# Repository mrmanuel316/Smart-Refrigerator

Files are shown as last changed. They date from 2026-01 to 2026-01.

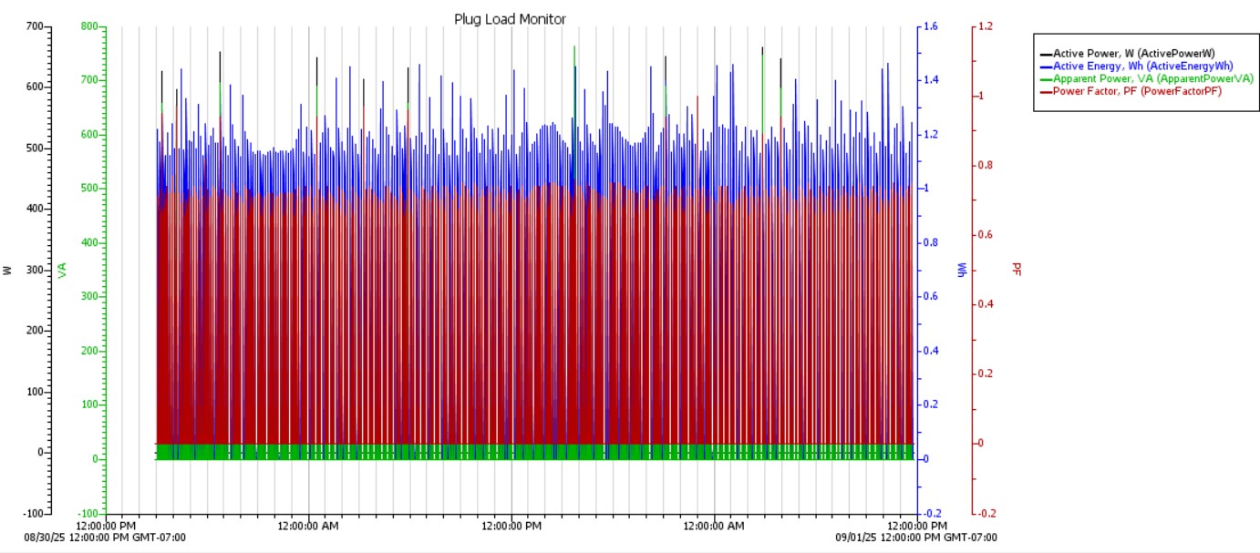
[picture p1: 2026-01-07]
Smart Refrigerator/Testing/Energy Performance/Only at Lvl 3 Power/First Test - No Bottle No Open/power graph.jpg

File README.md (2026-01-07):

# Smart Refrigerator – Passive Cooling Control System

## Demo Video
Watch the demo video on YouTube: [Smart Refrigerator Demo](https://youtu.be/O7e8nfwptJs)

## Overview
This project is an Arduino-based **Smart Refrigerator** system that automates cooling using fan-assisted heat dissipation and user-defined timing. It monitors temperature, controls fans, and provides real-time feedback through a digital display and buttons. The system is designed to improve energy efficiency during peak utility periods while maintaining safe internal temperatures.

## Project Objectives
- Automate cooling using fans and heatsinks  
- Monitor internal temperature in real time  
- Allow user input for time setting, manual override, and status control  
- Provide system feedback via digital display  
- Improve energy efficiency during peak usage periods  

## Hardware Components
- Arduino microcontroller  
- Temperature sensor (e.g., DS18B20)  
- Cooling fans and heatsinks  
- Digital display (7-segment or LCD)  
- Push buttons for time set, override, and control  
- Relays or transistor drivers  
- Power supply and wiring  

## Software and Tools
- Arduino IDE  
- C/C++ (Arduino)  
- Libraries for display and input handling  

## Data and Results
All experimental data, including temperature logs and performance results, are located in the `data/` folder (`Temperature_Data.xlsx`).

## Demonstration Videos
- Demo video stored locally: `media/Videos/Demo.mp4`  
- YouTube demo available at the top of this README.

## Project Images
Photos of the hardware setup, circuit, and final assembly are stored in `media/Images/`.

## Presentation Slides and Report
- Final technical report: `docs/Final_Report.pdf`  
- Presentation slides: `docs/Slides.pdf`  

## How It Works
1. Temperature sensor continuously monitors internal temperature  
2. Arduino reads the sensor data and compares it to predefined thresholds  
3. Fans activate automatically when cooling is required  
4. Users can manually set timing or override system using buttons  
5. System status and timing displayed in real time  
6. Safety logic prevents overheating or unsafe operation  

## Author
**Matthew Rabeje Manuel**  
Mechanical Engineering – San José State University  
Email: m.rmanuel003@gmail.com

## License
This project is for educational purposes. Free to use and modify with credit.

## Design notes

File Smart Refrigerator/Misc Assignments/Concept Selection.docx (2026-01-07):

Smart Refrigerator Concept Selection

Ideas considered for concept selection

Our group had a lot of ideas on how to execute building a mini fridge with a passive and active cycle. Some of the areas with the most variation were the fin and ice configuration, where in respect to the rest of the fridge would the fins, ice, and fans be located, as well as where to place our more complex control panel. During the concept creation phase, we had a lot of different ideas on how best to execute our envisioned project. However, there was a lot of overlap between designs, so it was quite easy to consolidate them to three or four well developed ideas. One way we consolidated or eliminated ideas was through evaluating the manufacturing cost. It was easy to get creative with different ice and fin designs, including circular tubes or curved banks of fins. However, once our group evaluated from a manufacturing perspective, some of our more abstract, yet efficient designs were eliminated.

After consolidating and eliminating ideas, we began to start discussing our options for the primary design decisions such as heat transfer shapes to contain our passive cooling ice block, control panel functions and placement, shelf designs, location and format of the control panel, and control panel location.

Control Panel Location

A control panel/apparatus is required for consumer use and monitoring. We plan to have a very simple setup where a user can see when their refrigerator is running an active/passive cycle, and we also plan to add a way for them to possibly override the passive cooling if desired. The control panel could be located on the front of the fridge, on the door of the fridge inside, or above the fridge door. Figure 1 shows three possible locations for our control panel.

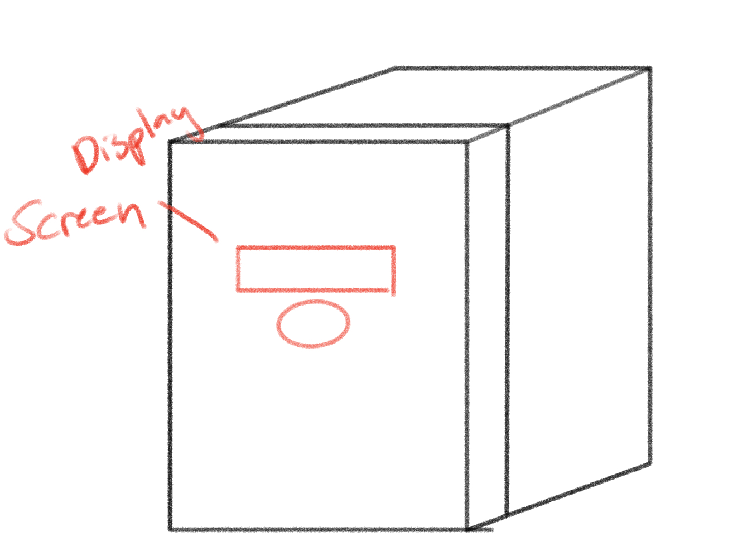
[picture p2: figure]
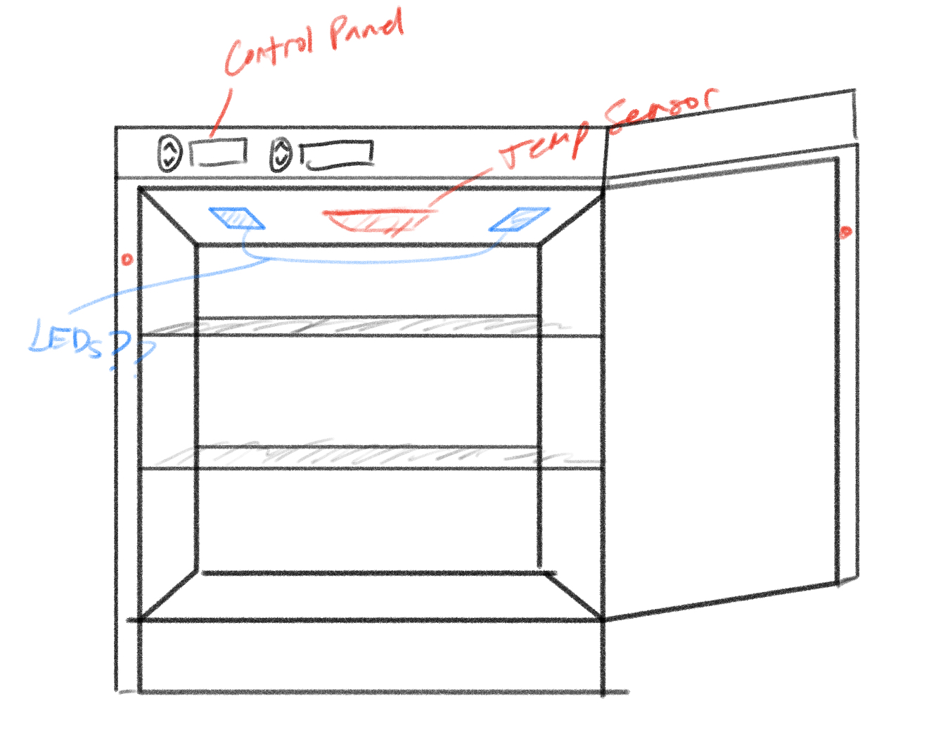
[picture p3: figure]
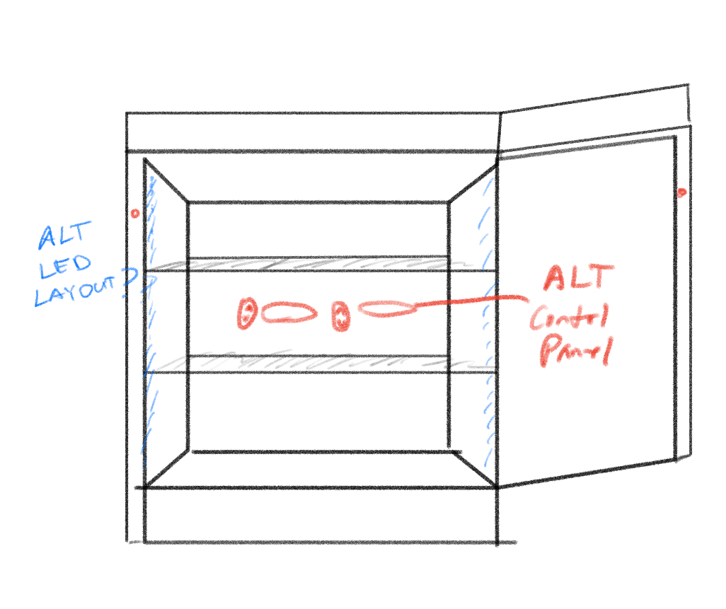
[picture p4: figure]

Figure 1. Alternative placement locations for refrigerators control panel

Control Display Layout

In our initial concept generation, we only had one concept generated for our potential control panel display layout as seen in Figure 2, so we just discussed how we would modify it to ensure we knew exactly what we wanted for our final design. To meet customer needs and make our fridge user friendly, a good control panel is needed, so we considered using lights, seven segments, or a LED screen.

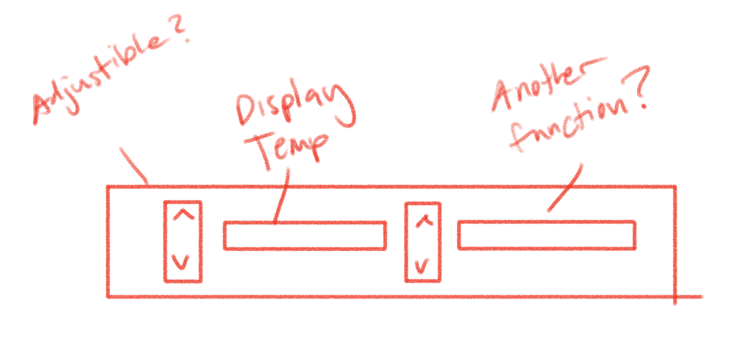
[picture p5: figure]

Figure 2 - Potential Display layout 1

Shelf Layout

During our customer needs survey, shelving and interior space was the most important metric for all respondents. Practically speaking, consumers want refrigerators to store food, so high-volume and convenient storage is important. With that said, the easiest way to optimize space for the consumer is to find an ideal shelving layout for our fridge. We introduced two options shown in figure three that have promise. Option one contains two bottom shelves, one large shelf, and one narrow shelf where option two contained two removable shelves, one drawer, a compartment for compressor/refrigerator components in the back, and rails for shelf adjustment.

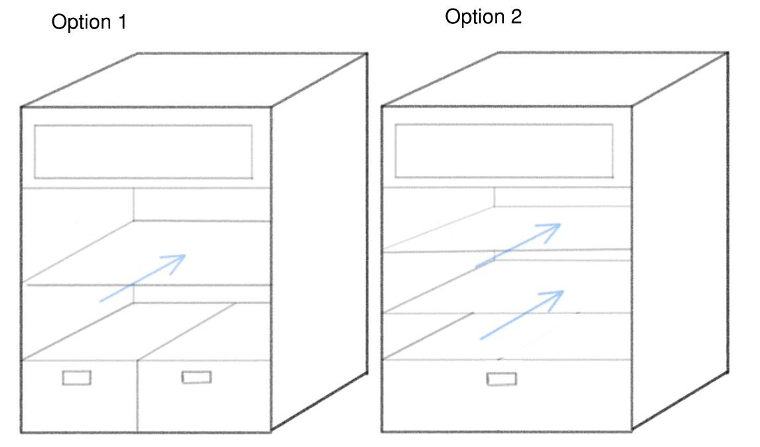
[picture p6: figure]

Figure 3 - Shelf Layout Options

Heat transfer Design

For the passive cooling cycle to provide effective cooling, air from the refrigerator must be cycled through a freezer compartment and cooled to below refrigeration temperature before it re-enters the refrigeration compartment. For cooling to occur, the air must interact with a medium that is at a lower temperature than the air itself such as ice. Only blowing air over ice would decrease the temperature of the air but is limited by the surface area. To increase the surface area and therefore improve the amount of heat transfer that occurs, fins made out of a highly conductive metal can be used. All blocks of ice will be similar to ice packs such that there will be water sealed inside a case with a gap of air so that the water can expand when it freezes and be contained when it melts.

We generated many different concepts for the form of the heat transfer component and created CAD models to better visualize and evaluate the designs. These concepts were constrained by whether the freezer compartment was located on top of the refrigeration compartment, increasing the refrigerator’s height or behind it, increasing the required floor space. Design 1 and Design 2 shown below in Figure 5 showcase the configuration where the freezer compartment is located on top of the refrigerator. Design 1 has one large slab of ice with a panel of fins located on the top and bottom. There would be a metal plate that constrains the air to flow either above or below the ice block through the fins. Design 2 is similar but instead uses several thin sheets of ice rather than one large block. This allows for more surface area to install fins and allow for air to flow through.

Design 3 through Design 5 showcase the configuration where the freezer compartment is located at the back of the refrigerator. Similar to Design 2, Design 3 includes several thinner sheets of ice with fins between. However, in Design 3 the sheets of ice are vertical. Though the vertical design allows for more surface area for heat transfer to occur, ice freezes much faster when it is placed in horizontal configurations. For this reason, Design 4 and 5 direct the airflow in a serpentine pattern such that the slabs of ice can be placed horizontally. Triangle wedges are used in the corners to decrease the backflow and pressure drop. Design 4 uses rectangular while Design 5 uses circular tubes.

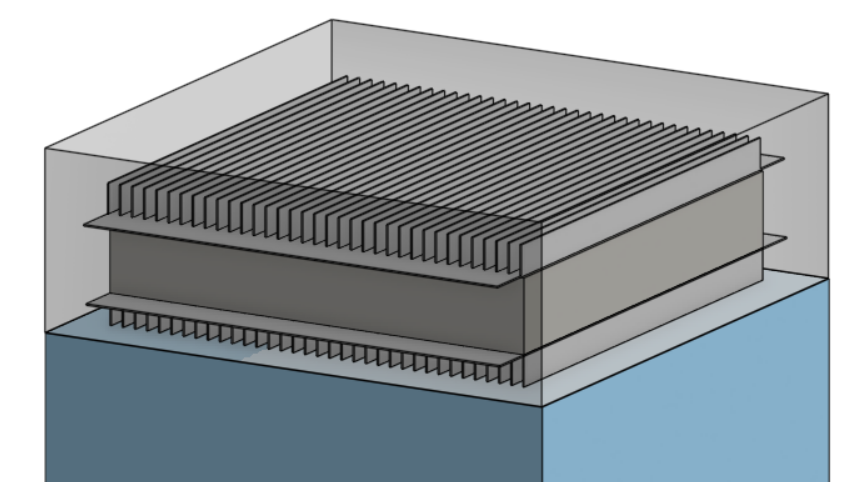
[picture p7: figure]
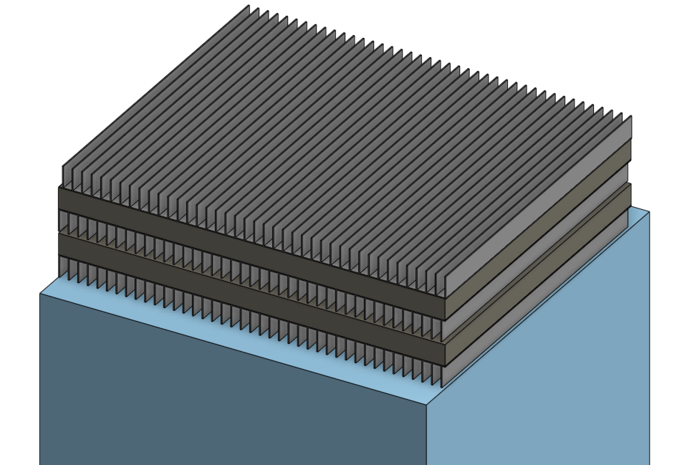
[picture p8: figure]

Design 1 | Design 2

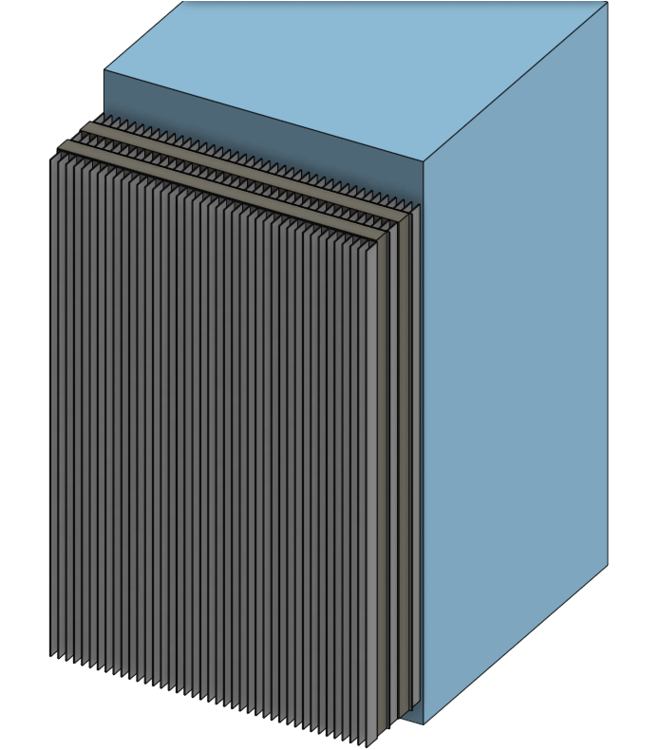
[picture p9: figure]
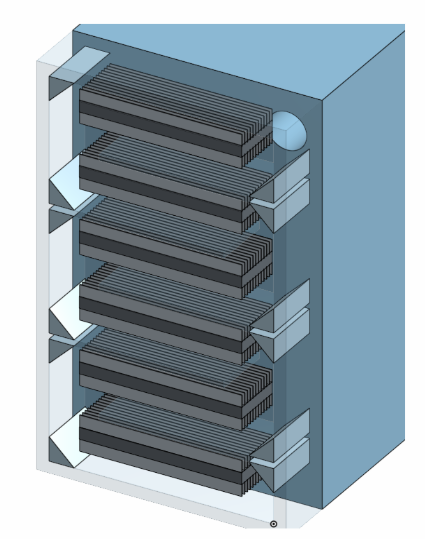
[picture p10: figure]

Design 3 | Design 4

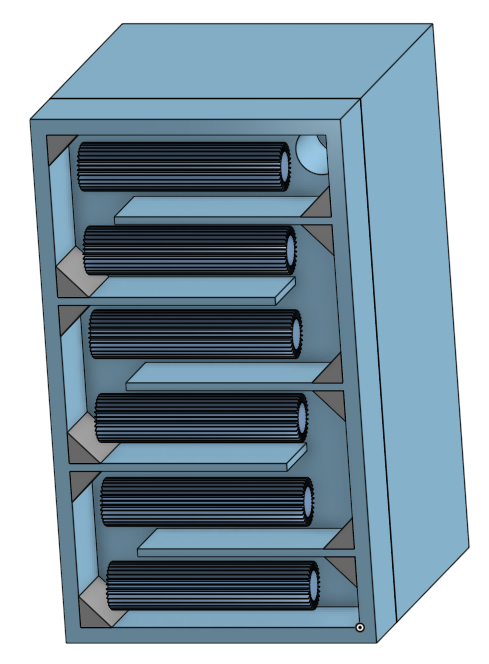
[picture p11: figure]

Design 5

Figure 4 - Heat transfer layout options

Decision Method used

Heat transfer

To choose which design was best for the heat transfer between ice and air, we used a Pugh matrix shown below in Table 1. We wanted to zero in on only the most relevant criteria that would affect feasibility of the project, such as manufacturability, efficient use of space, and heat transfer effectiveness. In terms of manufacturability, we found that most fins that can be purchased are meant to be installed on flat surfaces. This means that wrapping fins around a circular tube such as in Design 5 would be very difficult. Furthermore, we recognize that the serpentine pattern in Design 4 and 5 would be more challenging to construct compared to the simpler stack configuration in Design 1-3.

Since the passive cooling system relies on having a block of ice, the water must be frozen during the active cooling mode. To provide a net negative in energy consumption, the ice must be frozen and with as little energy as possible. For this reason, one of our criteria in the Pugh chart is how quickly the ice will freeze. This is dependent on the thickness of the block, the shape (rectangular vs circular) as well as the orientation of the block (horizontal vs vertical). Since Design 2 and Design 4 used thin, rectangular blocks that were horizontal, they had the best ice freezing rate and were awarded positive points accordingly. Though Design 1 is also rectangular and horizontal, freezing one large block rather than multiple thin layers will take longer.

Another aspect of the effectiveness of our refrigerator is how much electricity the system will consume during peak hours while the system is in passive cooling mode. During this mode, the only component that will be active is a fan that pushes air through the freezer compartment to decrease its temperature. The size of the fan will be dependent on the airflow pattern as well as how much surface area is available in the fins for heat transfer to occur. Design 1-3 all have simple airflow patterns which is ideal. The serpentine aspect of Design 4 and 5, however, is poor for airflow and would require a larger motor on the fan to overcome the loss in static pressure due to the turbulence in the turns. The size of the fan is also dependent on the fin surface area because increasing the surface area that is available for heat transfer to occur will cause the outlet temperature to be lower. The refrigerator will require less air circulation if it is supplied at a cooler temperature, allowing the fan to run at a lower speed and draw less electricity. For this reason, Design 2 - 4 which all had thin layers with lots of fin surface area are more desirable for our final design.

Finally, the amount of space that the freezer compartment requires is very important as it relates to the amount of usable interior storage space given a limited exterior size. From our evaluation of customer needs, it is clear that adequate interior space is very important for our customers. Since the ice blocks in Design 1-3 are pressed between fins with no wasted space or additional structure required, they make the most efficient use of space compared to Design 4-5. From the Pugh Chart, it is clear that the most ideal design is Design 2 with 5 points followed by Design 3 with 4 points. For this reason, we have chosen to move forward with Design 2.

Table 1: Pugh matrix for Heat Transfer Shapes

Criteria | Baseline/ Datum | Design 1 | Design 2 | Design 3 | Design 4 | Design 5
Ice freezing rate | 0 | 0 | +1 | -1 | +1 | -1
Fin Surface Area | 0 | -1 | +1 | +1 | +1 | 0
Manufacturability | 0 | +1 | +1 | +1 | 0 | -1
Efficient Use of Space | 0 | +1 | +1 | +1 | 0 | 0
Airflow Pattern/Static Pressure | 0 | +1 | +1 | +1 | -1 | -1
Total | | 2 | 5 | 4 | 1 | -3
Rank | | 3rd | 1st | 2nd | 4th | 5th

Control Panel

One of the main methods we used to determine the location of the control panel was to insert images from our concept generation into this document, organize them to better understand our options for each concept, and discuss what we think would work best for us in conjunction with our customer needs. Since we unanimously agreed that the best location for the control panel was located inside the refrigerator near the top of the refrigeration compartment, we didn’t need to use a decision making tool such as the Pugh Matrix.

To decide which indicators and controls should be included, we discussed the necessary interactions required between the microcontroller and the user. Since temperature control was not highly prioritized in our customer needs, we decided the control panel did not need up or down arrow buttons. The only inputs that are crucial for operation are that the user can tell the refrigerator when their utility rates and set the clock to accurately match the local time. The additional display features were then evaluated based on how crucial they were and what the user would like to know to troubleshoot any issues they encounter.

Shelf layout

To evaluate all of our shelf layout options, we placed the images side by side and discussed the pros and cons of each option. We once again referred to our customer needs and the importance of both the interior storage space and flexibility in shelving layout. When narrowing down our shelf design options, we also took into consideration the current shelf design of the broken mini fridge that we will be using as a starting point for our construction.

Final Concept

The final fin and ice configuration our group decided on was Design 2 for the freezer compartment. We chose this design using the Pugh chart as it had the highest score due to the high fin surface area, ideal freezing time, good airflow, efficient use of space and ease of constructability.

Figure 5 - Final design choice for fin and ice configuration

For the control panel configuration, we opted to not have user input for temperature. Because of the nature of our design, our refrigerator will not have a freezer, it will only keep things cold, so we felt user input was redundant to set temperature, our smart refrigerator will be programmed to maintain an internal temperature of 37 degrees fahrenheit. We did deem it important that our control panel will display the internal temperature. We also concluded it necessary for the control panel to indicate whether our project is on its active or passive cycle, which will be done with LED lights.

Lastly, for the user to configure when they want the passive cycle to run, we concluded on a design similar to conventional alarm clocks. We will have three time setting buttons, and two time adjustment buttons. The two time adjustment buttons are ‘hour’ and ‘minute’ and will be used to move the time around. The ‘clock set’ button will be used to set the primary clock time, this is the time that the passive cycle will start and end on. The user then will choose when they want the passive cycle to start and end. After discussing all the necessities for our control panel display, we came up with the display layout in figure 6.

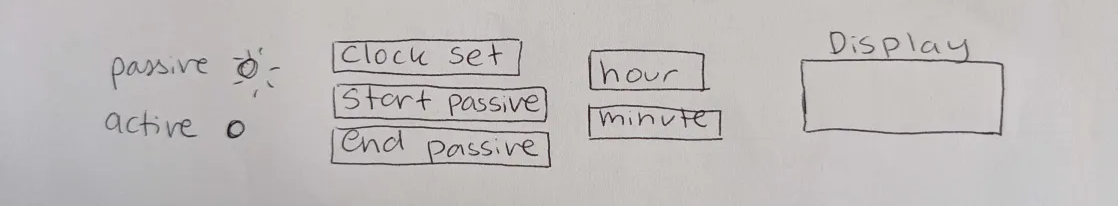
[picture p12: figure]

Figure 6 - Final control panel configuration

We also ultimately determined that the control panel should be placed on the top inside lip of the fridge as this is most custom and what most users are used to already as shown below in Figure 7.

Figure 7 - Final control panel location

For the shelving configuration, we decided to have two removable shelves and one single large drawer at the bottom shown below in Figure 8. This allows for the user to customize their refrigerator layout to best suit which items they regularly purchase and store. Furthermore, the single larger drawer rather than the two smaller drawers is better suited for our design because of the scale of the mini refrigerator we are working with.

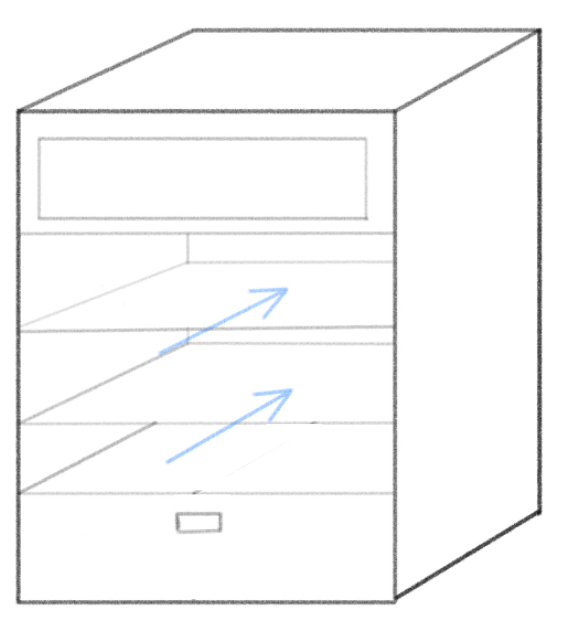
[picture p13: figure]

Figure 8 - Final shelf configuration

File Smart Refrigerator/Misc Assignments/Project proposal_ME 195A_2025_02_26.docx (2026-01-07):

Project Proposal

ME 195A, Spring 2025

Smart Refrigerator

Faculty Advisor: Dr. Keith Yi, keith.yi@sjsu.edu

Technical Advisor: Dr. Kabbani, hussameddine.kabbani@sjsu.edu

# Student Team Members (name, phone#, email)

1. | Isabel Price (team lead) | (669) 333-1464 | isabel.price@sjsu.edu
2. | Brent Marin | (650) 293-1821 | brent.marin@sjsu.edu
3. | Caleb Mok | (408)-309-3238 | caleb.mok@sjsu.edu
4. | Kalino Ruiz | (669) 333-1462 | kalino.ruiz@sjsu.edu
5. | Matthew Manuel | (408)-316-1427 | matthew.manuel@sjsu.edu

# Student Team:

1. Isabel Price | | | 3/18/2025
2. Brent Marin | | | 3/18/2025
3. Caleb Mok | | | 3/18/2025
4. Kalino Ruiz | | | 3/18/2025
5. Matthew Manuel | | | 3/18/2025

1. Introduction

With the knowledge we now have about various environmental problems centered around climate change, it is our duty to create a sustainable world and minimize our carbon footprint. One way we can do this is by reducing the average household energy expenses with the help of energy efficient appliances. By leveraging active and passive refrigerating techniques, we can incorporate a local ice storage system into a refrigerator that will generate ice during off peak hours which will maintain the internal temperature of the fridge during hours of peak electricity rates. Utility rates are how much we are charged for energy. When utility rates are higher during peak hours, we aim to use the passive cooling method to save the user money. The smart refrigerator intends to provide users with an eco-friendly and affordable option by decreasing utility rates and energy consumption.

2. Project Objectives

Our primary objectives include:

- Make an affordable, energy-efficient, and cost saving refrigerator
- The refrigerator must have easy to clean removable shelves
- A microcontroller will control the state of the refrigeration cycle

We want to build or repurpose a mini refrigerator that has an active and passive cooling cycle. The passive cycle relies on the principle of stored thermal mass to limit consuming energy during peak-load hours to save the consumer money. As a group we decided that our project will not be a success unless both active and passive cooling cycles work effectively. Lastly we want to retain as much of the original insulation in our mini refrigerator.

3. Customer Requirements

As a group we conducted a survey to get feedback on what people are looking for regarding refrigerators. We had 22 responses, with ages from 18 to 55+, about 54% of our responses were women and the rest were men. Once we received our input, as a team, each group member weighed each need on their own. The three highest customer needs for a refrigerator were: interior storage space, durability, and that it is easy to clean. Within our team, the three highest needs were interior storage space, the cost of the product, and the energy usage. The full customer needs results can be found below in Appendix B.

4. Background Research

Though there are not any currently commercially available refrigerators with integrated passive cooling methods, there have been studies conducted on refrigerator prototypes, refrigerated transport boxes, and air conditioning systems that use various methods of passive cooling. Garber-Slaght of the Cold Climate Housing Research Center conducted an experiment comparing regular refrigerators to a prototype unit with thermal fins located outside of the building, exposed to the winter conditions (2013). The results showed that the retrofit prototype unit used 6.3 kWh compared to 36.1 kWh for the regular units during the winter, though it underperformed during the summer due to the fins absorbing additional heat rather than cooling. This shows that passive refrigerator models can be effective in saving consumers money.

Other technologies and prototypes exist that use thermal mass as a means of either maintaining refrigerated temperatures for durations of time. Fauer and Cremaschi developed a transport box for blood bags that successfully maintained the temperature between 2 and 6 ℃ for an extended period of time using only phase change materials as a form of thermal mass (2024). Our Smart Refrigerator will be a combination of these technologies as it will integrate the thermal mass method of refrigeration boxes into the typical form of a refrigerator with a refrigerant loop and compressor.

5. Design Constraints

There are four main constraints regarding our project. They are: budget limitations, material availability, safe operation, and sound levels produced. Funding is limited from our sponsors and the members of this group have a limit they are willing to spend individually. Regarding the construction of the insulation of our project, some materials are far better at insulating heat than others, but are not always readily available for sale to the public nor cheap. When it comes to prototyping our project, consumer safety is our number one priority so we will be avoiding flammable refrigerants.Our last constraint is sound level, this mainly pertains to the compressor. While it may be more cost and power efficient to go with a cheap, large, or low quality compressor, we want to design a product that consumers will use and not notice.

6. Project Plan & Gantt Chart

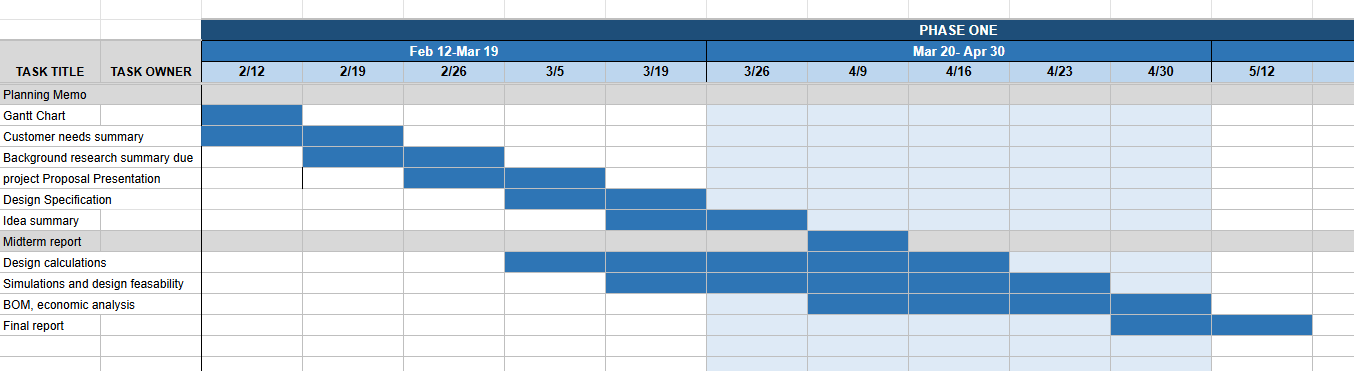
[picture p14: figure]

We aim to work as a team toward the final report for the semester. Our work is currently split between technical leads who will be in charge of CAD, heat transfer calculations, fabrication, code, the refrigeration cycle, and mechatronics/sensing. We still plan to have all team members help each other on their lead assignments. Strong communication is a cornerstone of all work to be done. Our general strategy is to work ahead of time on as many assignments as is reasonably possible, which is why we have already started rough design calculations and economic analysis, as both go hand-in-hand with testing the viability of our project.

References

Fauer, C., & Cremaschi, L. (2024). Passive cooling of two phase change materials installed in series. International Journal of Refrigeration, 159, 124–133. https://doi.org/10.1016/j.ijrefrig.2023.12.024

Garber-Slaght, R. (2013, March). Passive Refrigeration. Cold Climate Housing Research Center; CCHRC. https://cchrc.org/wp-content/uploads/media/passiverefrigeration.pdf

Appendices

A. Mission Statement
B. Customer Needs Summary
C. Teamwork Plan

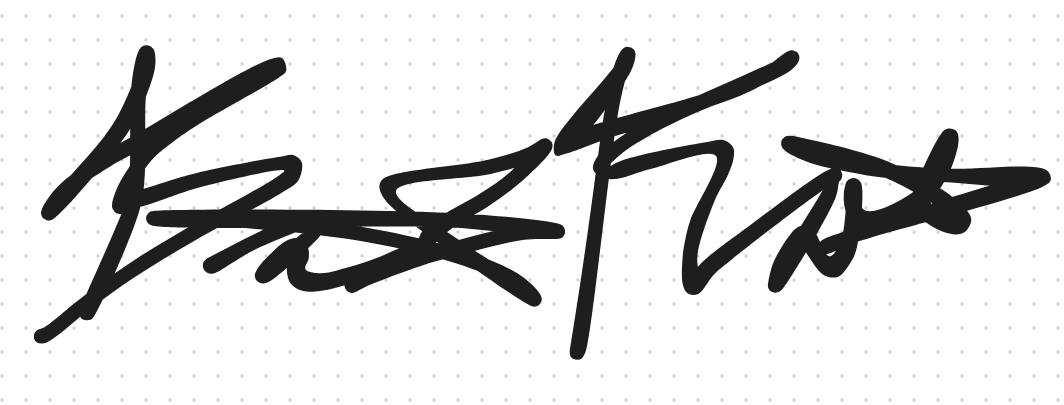
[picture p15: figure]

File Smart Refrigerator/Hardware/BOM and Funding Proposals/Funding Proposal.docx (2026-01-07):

Smart Refrigerator

Isabel Price, Kalino Ruiz, Matthew Manuel, Brent Marin, Caleb Mok

ME 195A Section 02

Instructor: Dr. Keith Yi

Technical Advisor: N/A

5/9/2025

Executive Summary

In California, the cost of electricity is continuously rising, leading to more households and individuals being unable to afford their electricity bills. Typical rate schedules for electricity costs have a peak period in which the price of electricity is increased due to the high demand during that time of the day. One method of reducing electricity cost in cooling systems is to shift the consumption of electricity from the peak time to off-peak through thermal mass.

Our product, the Smart Refrigerator, is a mini refrigerator that utilizes thermal mass in the freezer chamber with the purpose of shifting electricity consumption from peak to off-peak periods to save the user money. This prototype will involve the retrofitting of an existing mini refrigerator. Our goal is to successfully integrate the passive cooling system involving the thermal mass, heat sinks, and fans, with the existing active refrigeration system such that the refrigerator can still operate regularly during off-peak hours.

The mini refrigerator will be controlled with a microcontroller that will monitor temperatures throughout the chamber and control the switch between the active and passive cooling modes based on the user's rate schedule. Our expected outcome is a fully operational mini refrigerator that responds to user inputs for their personal rate schedule. The project will be successful if both the unmodified active refrigeration system and the added passive refrigeration system maintain a refrigeration temperature of 37 degrees and provide cost savings for the user.

Anticipated Deliverables

Our final anticipated deliverable is the physical prototype of the retrofitted mini refrigerator that is capable of using passive cooling for several hours a day and maintains the storage chamber at a safe refrigeration temperature. This fabrication process can be broken down into smaller deliverables including the repair of the existing broken mini refrigerator we are retrofitting, the lowering of the freezer compartment, construction of the heat sink and ice block assembly, and the installation of the various aluminum plates to direct air flow. Furthermore, the implementation of the microcontroller and sensors to effectively monitor the temperatures and control the refrigerator is an important step in the process. Along with the prototype, we will also provide data on the performance and energy cost savings to evaluate the success of the project.

This product will be beneficial for those who are interested in saving money on electricity throughout the year. It will be most cost-effective in states where electricity is expensive, such as in Hawaii or California. Furthermore, the Smart Refrigerator offers a cost-saving solution for college students and other young renters who are more likely to use a mini refrigerator and are particularly vulnerable to high electricity bills due to lower or inconsistent income.

Brief description and the most recent illustration of your latest design

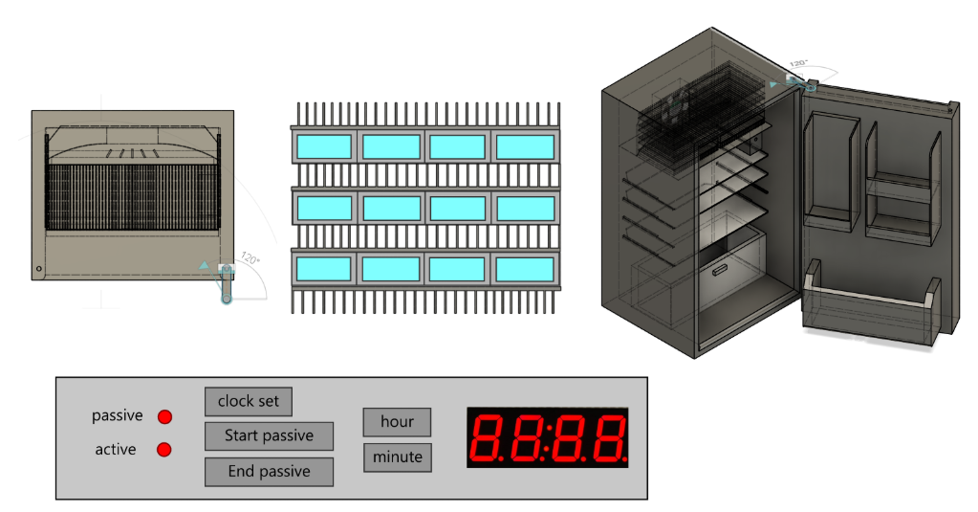
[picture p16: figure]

Figure 1 - Smart Refrigerator final design including freezer compartment layout, fin and ice block assembly, retrofitted mini refrigerator, and control panel layout

Our smart refrigerator will be programmed to maintain an internal temperature of 37 degrees Fahrenheit. We determined that the control panel should be placed on the top inside lip of the fridge, as this is what is most common. We will also be using LED lights for the control panel to indicate whether our project is on its active or passive cycle. The user will also be able to configure when they want the passive cycle to start and end with time setting adjustment buttons which work similarly to an alarm clock. There will also be LED lights that indicate whether it is on its active or passive cycle. Our control panel design layout is shown in the bottom image of Figure 1.

For the fin and ice configuration, our group decided on the design in the image in the middle. There will be four layers of fins to enhance heat transfer, along with three layers of ice to maintain the surface temperature at 0 degrees Celsius. For the ice containers, we will be using aluminum rectangular tubing with four individual tubes for each of the three thermal mass layers.

Since we will be using the freezer section for our thermal mass and passive cycle, we decided to direct airflow with a fan through the middle of the top back panel of the freezer to maximize convection. To further direct and smooth the air flow, we will also be using five vanes and curved sheet metal at the fan opening. This layout is shown in the top left corner of Figure 1.

Project Budget and complete rationale

Table 1 - Bill of Materials

Component Name | MFG# | Description/ Purpose | Quantity | Cost/ Unit | Shipping | Total | Notes | Link
Fan | SP100A | 4.68 Inch AC Tube Axial | 1 | 13.95 | $ 9.18 | $ 23.13 | Meets CFM requirement | Link (https://www.jameco.com/z/SP100A-1123XBT-GN-Sunon-120mm-115-VAC-60Hz-Ball-Bearing-Fan-240mA-20W-117-CFM_102884.html)
R134a Recharge kit | B09S69H5DP | To pressurize and add pipe length | 1 | 20.99 | $ - | $ 20.99 | Will need can of R-134a | Link (https://www.amazon.com/FANOVO-Refrigerator-Recharge-Refrigerant-Self-Sealing/dp/B09S69H5DP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)
R-134A | SER134A | Pure R-134A | 1 | 14.00 | $ 11.32 | $ 25.32 | | Link (https://coldhose.com/products/r134a-refrigerant-12oz-can?variant=35532320014496)
Copper Pipe | 630456606893 | Refrigerant Piping 3/8" OD | 1 | 16.99 | $ - | $ 16.99 | 5 Feet of tubing | Link (https://www.amazon.com/GOORY-Copper-Tubing-0-328-Refrigeration/dp/B0DKT3JDPT)
Heatsink | 64AS | 7.874'' (200mm) Wide Heatsink (64AS) | 8 | 9.90 | $ 12.36 | $ 91.56 | 7.9" x 6" | Link (https://heatsinkonline.com/products/7874-wide-heatsink-64as?variant=42105916653730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)
Temperature Sensor | ERP 2188820 | Refrigerator Thermistor | 2 | 11.00 | $ - | $ 22.00 | | Link (https://www.amazon.com/ER2188820-ERP-Thermistor-Replaces-2188820/dp/B01M8OFHHX)
Display | TM1637 | 4 Digit 7 Segment Display | 1 | 3.95 | $ 4.09 | $ 8.04 | | Link (https://www.jameco.com/z/TM1637-JVP-Jameco-ValuePro-TM1637-4-Bits-Digital-Red-LED-Display-Module-for-Arduino-7-Segment-0-36-4-Digit-Clock-Anode-Serial-Driver-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)
Buttons | EK1019 | 6x6x4.3mm TACT Switch Push Button | 1 | 6.98 | $ - | $ 6.98 | (pack of 50) Purchasing separately | link (https://www.amazon.com/Gikfun-6x6x5mm-Switch-Button-Arduino/dp/B00R17XUFC?gQT=2)
Aluminum Tube | T34118 | Ice casings | 12 | 9.30 | $ 41.00 | $ 152.60 | 4x1x1/8"x6 Note this shipping rate covers both the tube and sheets | Link (https://www.metalsdepot.com/aluminum-products/aluminum-rectangle-tube?product=290)
Sheet Aluminum | S3063 | Ice Casings/ controlling airflow | 2 | 42.72 | | $ 85.44 | 24"x24"x1/16" | link (https://www.metalsdepot.com/aluminum-products/aluminum-sheet?product=381)
Microcontroller | ESP32 | Control the Fridge | 1 | 8.00 | $ - | $ 8.00 | Already owned | link (https://www.espressif.com/en/products/socs/esp32)

Total including already purchased buttons and microcontroller: $461.05

Total funding requested from the department: $446.07

Part justifications

Heat sink selection

After comparing calculations with and without a heat sink, we determined that a heat sink is required to provide adequate heat transfer between the ice block and the air passing through the freezer compartment. There were many factors involved in choosing the optimal heat sink, including the size restrictions of the small freezer compartment we were working with, the length vs width orientation of the heat sink, as well as the minimum airflow to achieve the desired heat transfer. To determine the required heat transfer to maintain refrigeration temperature, we calculated the heat transfer through the walls of the refrigerator in addition to the added groceries that were stimulated by the energy required to take cans of water from room temperature to refrigeration temperature. The load profile can be found below in Figure 2.

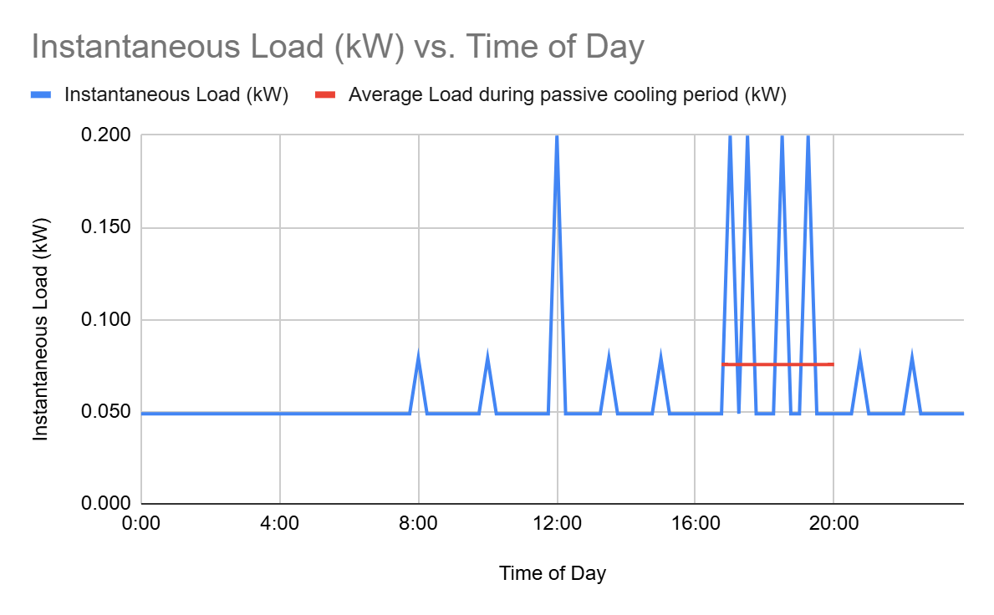
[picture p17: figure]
Chart

Figure 2 - Simulated instantaneous load on refrigerator cooling system

To choose the heat sink, we first created a tool in Google Sheets that used input dimensions of the heat sink and ice block, then calculated the resulting heat transfer given an input air flow rate. An example of the output calculations is shown below in Table 2. If the provided heat transfer rate was greater than the required heat transfer rate to maintain refrigeration temperature, the airflow was considered acceptable, as demonstrated by the green-filled cells in Table 2.

Table 2- Heat transfer calculations for heat sink

volumetric flow (CFM) | 20 | 30 | 50 | 55 | 60 | 70
V_dotTotal (m^3/s) | 0.00944 | 0.01416 | 0.02360 | 0.02596 | 0.02832 | 0.03304
Mdot Total (kg/s) | 0.01215 | 0.01822 | 0.03037 | 0.03340 | 0.03644 | 0.04251
V_dotPer fin (m^3/s) | 0.0000433 | 0.0000650 | 0.0001083 | 0.0001191 | 0.0001299 | 0.0001516
MdotPer fin (kg/s) | 0.000056 | 0.000084 | 0.000139 | 0.000153 | 0.000167 | 0.000195
Vair (m/s) | 0.408 | 0.612 | 1.020 | 1.122 | 1.224 | 1.427
Re | 295 | 442 | 737 | 811 | 885 | 1032
Flow | L | L | L | L | L | L
Entry Length | 0.156 | 0.233 | 0.389 | 0.428 | 0.467 | 0.545
Developed? | N | N | N | N | N | N
Nu | 4.42 | 4.74 | 5.30 | 5.43 | 5.55 | 5.79
h (W/m^2C) | 10.30 | 11.04 | 12.34 | 12.64 | 12.93 | 13.49
m | 4.06 | 4.20 | 4.44 | 4.50 | 4.55 | 4.64
fin efficiency | 88.94% | 88.26% | 87.08% | 86.82% | 86.57% | 86.08%
Toutlet (C) | 1.2 | 1.6 | 2.1 | 2.1 | 2.2 | 2.3
(Tbase-Tin) | 5.04 | 5.04 | 5.04 | 5.04 | 5.04 | 5.04
(Tout - Tsurf) | 1.1 | 1.5 | 2.0 | 2.1 | 2.2 | 2.3
Delta T LMTD | 2.6 | 3.0 | 3.3 | 3.4 | 3.4 | 3.5
Qfin, actual (W) | 31.9 | 38.5 | 47.4 | 49.2 | 50.8 | 53.9
Qdot diff | -18.60 | -12.02 | -3.11 | -1.33 | 0.33 | 3.38

The ultimate goal of this optimization process was to determine which heat sink had the best fin height, thickness, and spacing and how many layers of ice and fins were necessary to achieve a reasonable airflow rate. We chose the heat sink that had the optimal heat transfer when compared to six different heat sinks that varied in fin spacing and height. Next, we determined that three layers of ice were required with the chosen heat sink to obtain a reasonable average airflow rate of approximately 60 CFM.

Fan Selection

Before selecting our fan, we calculated the pressure drop at various air flow rates to create a system curve shown below in Figure 3. Then, we researched fans that had a maximum airflow rate that was about twice as large as our calculated average airflow. This would allow the passive system to respond to larger instantaneous loads and prevent the refrigerated space from exceeding the acceptable temperature range. We considered the fans' power consumption and size as these were the most important considerations. After choosing the fan that best met these criteria, we plotted the provided fan curve against our system curve to ensure that the fan was able to overcome the pressure drop it would encounter. Since the fan curve intersects the fan curve at a greater airflow than the minimum average airflow we calculated previously, we know that the fan will be adequate. We will modulate the fan to lower or higher speeds to meet the instantaneous airflow requirements.

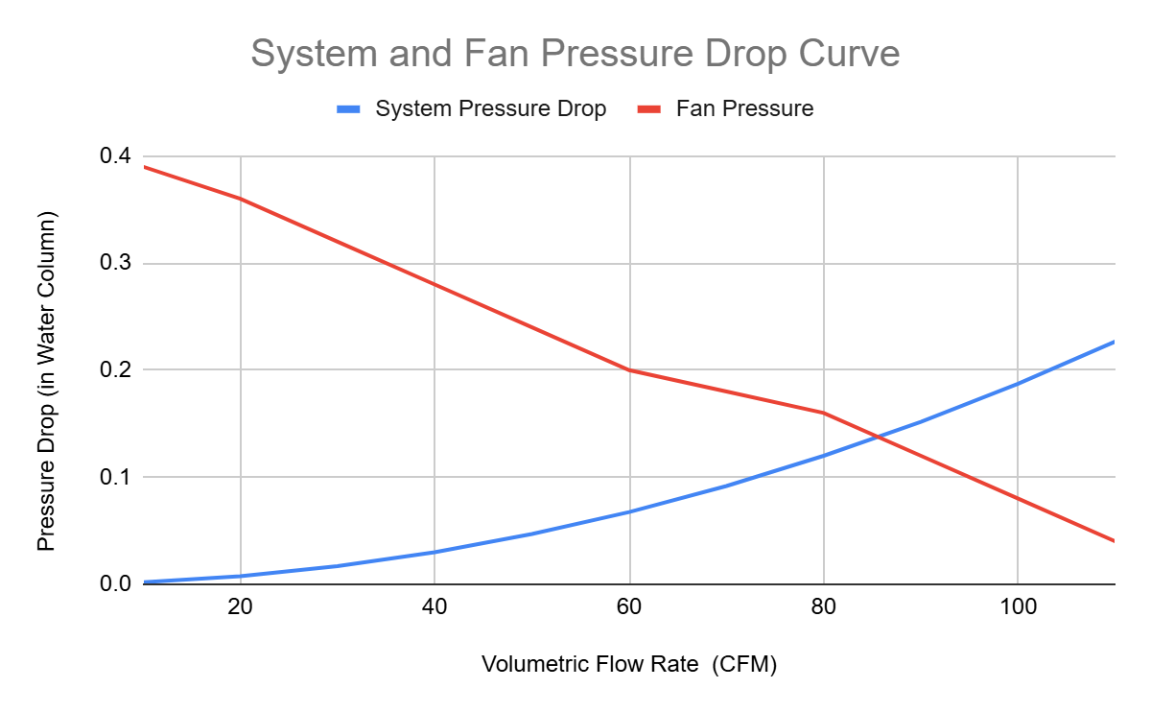
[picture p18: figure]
Chart

Figure 3 - System and Fan Pressure Curve

Ice Block Containers

We chose hollow aluminum tubes for our ice block containers instead of bending aluminum sheet metal for ease of fabrication and less potential for water leakage. By using tubing, we can create module ice cases by cutting the tube to the desired length, filling it with water, then welding an aluminum plate end cap on each end. We will utilize the aluminum plate for the end caps, as well as fashioning brackets to connect the fin/casing housings together in the freezer portion of our fridge. The last usages of our aluminum plate will be to create a return duct on the back wall of the inside of our mini refrigerator to return air to the fan to be cooled off during the passive cycle, as well as vanes and a wall to along the backside of the evaporator coils to direct airflow over the ice block casing assembly.

Electronic components

We decided to use the ESP32 microcontroller because of its vast capabilities and versatility. This microcontroller can be used as an efficient central processing unit capable of managing system inputs and outputs, sensors, and wireless communication. It is also a relatively fast processor with a speed of 240 MHz, which is more than sufficient for the system we’re planning to run. Additionally, it’s compatible with Arduino and MicroPython, the software that we’ve familiarized ourselves with in previous courses.

We chose the temperature sensors to be thermistors because of their high sensitivity to changes in temperature and their lower costs than alternative devices like thermocouples. Then we need a 7-segment display for our control panel that will display the time that the user selects for the start and stop of the passive cycle.

Return air ducting, fan ducting

To ensure that the air travels through all of the shelves rather than immediately re-entering the freezer compartment, we are installing a thin aluminum sheet to act as a return duct with a gap at the bottom of the refrigeration compartment. This requires a sheet of aluminum that will act as the return duct.

Within the freezer compartment itself, the air flow from the fan must be contained such that it flows through the fin + ice block assembly. To do this, we will be using aluminum sheets that are bent to fit into the corners of the freezer compartment. Furthermore, vanes will be used to disperse the fan flow to more equally distribute the flow through the individual fins. These vanes can be cut from the thin aluminum sheet as well.

Refrigerant piping

The freezer space in the mini refrigerator we are retrofitting only has a height of about 5 inches. However, the fin and ice block assembly has a height of 6.15 inches. In order for the fin and ice block assembly to fit, we must detach the evaporator coil and move it about 1.4 inches lower. We need a few inches of piping to account for this vertical translation. We chose the shortest amount of piping possible to save money; alas, the shortest length available was a 5-foot coil. In addition to this, because we are cutting the preexisting refrigerant piping, we need a way to pressurize and add more refrigerant after we drain it. We will be purchasing a kit that adds valves to hook up to a hose so that we can add refrigerant. This kit also comes with a pressure gauge, which will be very helpful so that we can ensure the compressor is operating smoothly. Lastly, we will be purchasing refrigerant to recharge the refrigerant line. Our mini-fridge requires 2.3 oz of R-134A, so we budgeted for a 12-oz. can.

Detailed Part List

The following is a list of the remaining parts that must be purchased for our project. Note that the microcontroller and buttons have already been purchased/owned by team members and do not need to be purchased by the department.

1. Aluminum Rectangle Tube
  a. Link (https://www.metalsdepot.com/aluminum-products/aluminum-rectangle-tube?product=290)
  b. Model: 4”x1”x1/8”
  c. Stock Number: T34118
  d. Dimensions: 4”x1” (1/ 8” thick) Choose cut to size, enter 6” Lengths
  e. Quantity: 12 Pieces
2. Aluminum Sheet
  a. Link (https://www.metalsdepot.com/aluminum-products/aluminum-sheet?product=381)
  b. Stock Number: S3063
  c. Dimensions: 2x2 Feet (1/16” thick)
  d. Quantity: 2
3. Aluminum heatsink
  a. Link (https://heatsinkonline.com/products/7874-wide-heatsink-64as?variant=42105916653730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)
  b. Model: 7.874'' (200mm) Wide Heatsink (64AS)
  c. Dimensions: Choose 6” length
  d. Quantity: 8
4. Refrigeration Piping Kit
  a. Link (https://www.amazon.com/FANOVO-Refrigerator-Recharge-Refrigerant-Self-Sealing/dp/B09S69H5DP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)
  b. Model: B09S69H5DP
  c. Dimensions: n/a
  d. Quantity: 1
5. Can of R-134A
  a. Link (https://coldhose.com/products/r134a-refrigerant-12oz-can?variant=35532320014496)
  b. Model: SER134A
  c. Dimensions: n/a
  d. Quantity: 1
6. Temperature Sensor
  a. Link (https://www.amazon.com/ER2188820-ERP-Thermistor-Replaces-2188820/dp/B01M8OFHHX)
  b. Model: ERP 2188820
  c. Dimensions: n/a
  d. Quantity: 2
7. Seven Segment Display
  a. Link (https://www.jameco.com/z/TM1637-JVP-Jameco-ValuePro-TM1637-4-Bits-Digital-Red-LED-Display-Module-for-Arduino-7-Segment-0-36-4-Digit-Clock-Anode-Serial-Driver-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)
  b. Model: TM1637
  c. Dimensions: n/a
  d. Quantity: 1
8. Fan
  a. Link (https://www.jameco.com/z/SP100A-1123XBT-GN-Sunon-120mm-115-VAC-60Hz-Ball-Bearing-Fan-240mA-20W-117-CFM_102884.html)
  b. Model: Sunon SP100A-1123XBT.GN
  c. Dimensions: 4.68 x 4.68 in
  d. Quantity: 1

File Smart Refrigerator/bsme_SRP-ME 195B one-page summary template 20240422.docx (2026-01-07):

Reducing Energy Costs Using Thermal Mass in Refrigerator

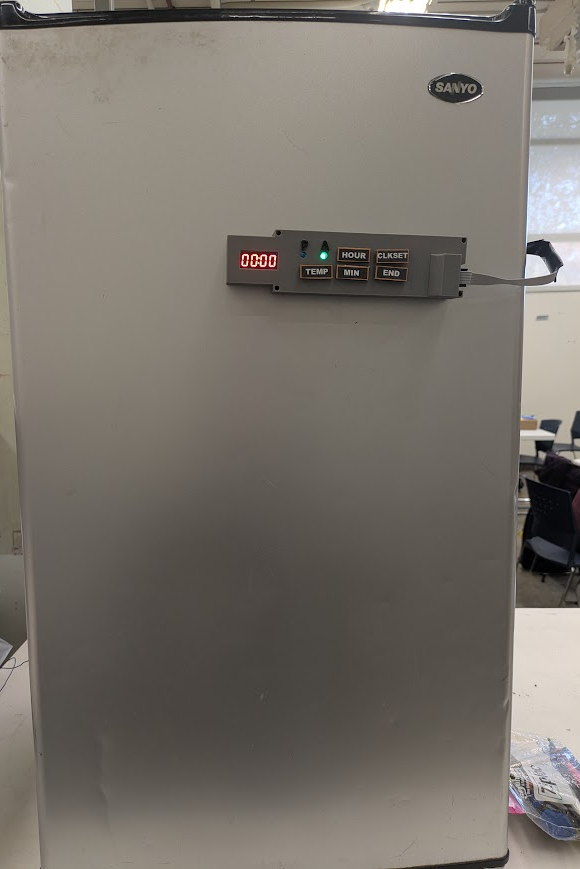
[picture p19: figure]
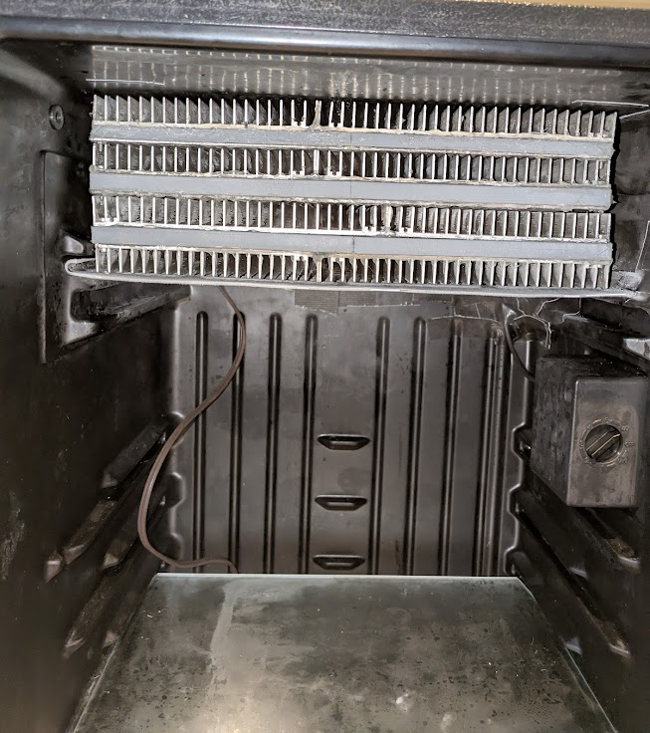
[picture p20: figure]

Student Team Members: Isabel Price (Lead) Matthew Manuel Brent Marin Caleb Mok Kalino Ruiz Faculty Advisors: Dr. Keith Yi Sargon Ishaya

Project Objectives:

We implemented a passive cycle assembly to a refrigerator that blows air over a thermal mass to maintain a safe internal temperature during the peak utility rates, reducing electricity cost, and a microcontroller to control the active and passive modes.

1. Utilize thermal storage to shift load away from peak time of use duration while maintaining safe refrigeration temperatures
2. Evaluate performance through energy consumption of both active and passive cooling cycles
3. Calculate money saved through minimizing energy usage during peak hours
4. Evaluate the air velocity profile of the passive cooling cycle

Significance:

This smart refrigerator improves environmental sustainability through reducing electricity load and carbon emissions during peak utility rate periods.

Project Results:

1. The fan successfully cycles on when the temperature is below 40°F until the chamber temperature lowers to 37°F.
2. The expected energy savings are 24.0 kWh/year based on initial tests.
3. The resulting cost savings are $12.60 per year.
4. The velocity profile was determined using an anemometer with an average velocity of 1.14 m/s.

Sponsors:

Thank you to Dr. Keith Yi, Sargon Ishaya, Desmond Cheung, Christopher Price, and Dr. Hussameddine Kabbani for their support throughout the design and fabrication of our senior design project.

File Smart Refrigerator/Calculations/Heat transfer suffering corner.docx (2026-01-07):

First step:

Estimate how volume of ice is required based on several different refrigeration load schedules

Step 2:

Create various different versions of the ice/fin model

Step 3:

For each version, determine fin surface area

https://www.mdpi.com/2079-6412/13/1/12

Step 4:

Determine if the fins can be considered constant temperature (find the temperature profile for fins of various lengths)

https://hedhme.com/content_map/?link_id=642&article_id=546

Although typical fin pitches are five to eight fins per centimeter, applications may exist for as many as 1,200 fins per meter in automotive applications. Fin thicknesses of 0.1–0.25 mm are common. Fin heights may range from 0.25 to 2 cm. A plate-fin exchanger with 600 fins per meter provides about 1,300 m²/m³ of heat transfer surface per cubic meter of volume. Such a heat exchanger would contain 10 times as much heat transfer surface per unit volume as in a typical shell-and-tube heat exchanger having 19 mm diameter tubes. Operated at a frontal velocity of 3 m/s, the heat transfer coefficient based on prime surface area would be on the order of 1,800 W/m² K.

Step 4:

Determine the heat transfer for given mass flow rate/outlet temperatures

Other things we need to figure out:

How are we going to tell the compressor when to turn on/off?

How are we going to control the power level of the compressor? (Duty Cycle - programming)

How are we going to control the power level of the fan? (Speed controller programming)

How will the air flow through the refrigerator

Where should the supply vent be located

How many vents should we use

Where should the return vent be located

What are we doing with the door of the refrigerator (shelves)

Are we going to put the heat exchanger in a new compartment on top of the refrigerator i inside the refrigerator (Kalino-y stuff)

Brent

- How do we freeze the ice

Matthew

- We need to make a circuit diagram that includes the fans, compressor, microcontroller, and sensors
- What microcontroller are we going to use?
- How is the microcontroller going to be powered
- We need to step down the voltage from the wall power supply
- We need a transformer?

Matthew

- Where should the temperature sensors be located?
- What type of temperature sensor should we use?
- How will the temperature sensor be installed?

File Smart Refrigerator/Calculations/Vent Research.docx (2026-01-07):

https://theappliancepros.ca/blog/refrigerator-return-air-vent/

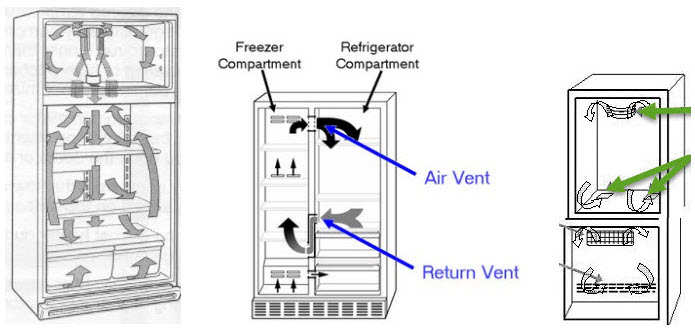
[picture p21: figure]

- PREDICTING AIRFLOW AND TEMPERATURE PATTERN INSIDE A REFRIGERATOR THROUGH CFD https://www.arpnjournals.org/jeas/research_papers/rp_2016/jeas_0716_4650.pdf

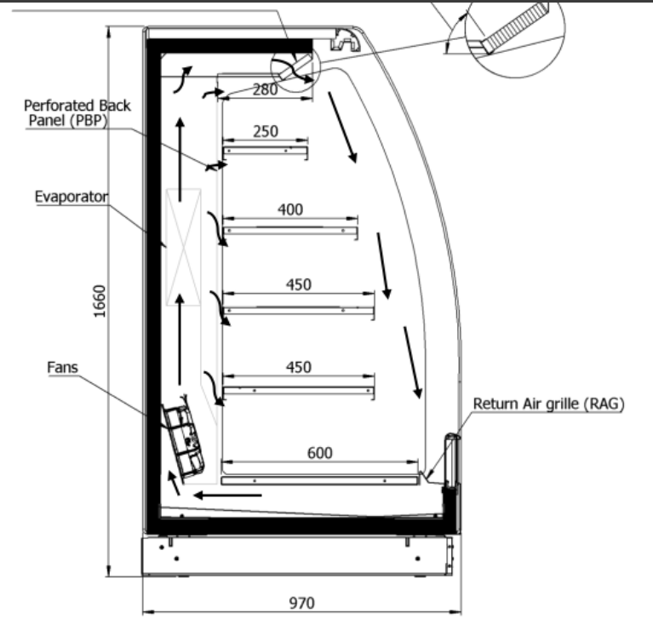
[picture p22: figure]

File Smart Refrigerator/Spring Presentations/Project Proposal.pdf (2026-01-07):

Cooling High-Power Dissipating Artificial Intelligence Chips Using Refrigerant

By: Waheeb Mukatash, Tyler Yang, Matthew Moscoso, Marc Massalt, Merari Mejia Robles,

Charlie Nino

Scope

We are trying to address the need for cooling high-power dissipating chips, particularly

AI chips. These chips consume more power than previous chips. Thus, we intend to design,

build, and test a vapor compression refrigeration cycle to analyze its efficiency in cooling 4 AI

chips. We will compare our prototype to previous research and provide steps to follow to

continue improving refrigeration for high-power dissipating chips.

Problem Statement

As developers transition to a realm of artificial intelligence, these high-performing

circuits will expose issues with existing cooling systems since they will not surmount the needed

output and productivity. Refrigeration cooling can directly provide solutions to pressing issues

such as limited power envelopes, high upfront expenses, system inefficiencies, as well as

industry sustainability. Current trends towards high performance computing shows that the

power consumption per chips and rack units are requiring more energy which will naturally

equate to more heat being generated and thus, more cooling being demanded.

More data is becoming readily available and must be processed on demand efficiently

and effectively. With flagship products such as NVIDIA's H100 supercomputing node requiring

upwards of 700W of power to reach maximum performance reveals the dire need to move

toward another cooling approach. In terms of performance, air cooling possesses the capabilities of only regulating 30 kW per rack with major inefficiencies [1]. With refrigeration cooling being

able to triple that capability by being able to cool 100kW per rack, the use of AI chips real-time

processing becomes possible to achieve smarter and quick computations through practically

unlimited cooling capabilities that the dielectric fluid provides. These future overworked

processors thus require a significant boost in cooling power and must be geared toward

decreasing leakage as well as evolving the power performance.

Introduction/Background

As of today, conditioning systems such as conventional air cooling and liquid cooling are

the primary systems used to regulate temperatures within high-powered chips. Computing chips

have evolved over time, requiring more power dissipation. In 2008, IBM introduced the Power

575 Supercomputing Node which offered a fully configured cooling processor that contained the

potential of dissipating 72 kW via water cooling. Most liquid cooling systems today mirror IBMs

processes dating even further than two decades back prompting a new revolutionary system.

NVIDIA's state-of-the-art and most commonly used GPU, H100, is used specifically for

Artificial Intelligence, AI, and includes 80 billion transistors. This equates to a 160% power

consumption increase from the previous generation’s chip [2]. Current cooling configurations

would require compatibility and optimization changes to effectively manage these unprecedented

heat loads. Our project is geared to focus on researching using a refrigeration cooling system to

cool high-power dissipating AI chips.

Technology’s next advancement, artificial intelligence, projects the future direction of

how engineers interact with automated engineering. Artificial intelligence is the basis of

computer algorithms to process information and mimic human intelligence which started in the early 1950s and led to machine learning technologies of today [3]. Some applications include

autonomous vehicles, voice assistants, automated predictions, modeling, facial recognition, and

many other useful applications. Over the years, the development of AI core chips has

experienced many changes as they originally started as a simple semiconductor to be able to

handle large amounts of data and be power efficient. Compared to traditional general-purpose

CPUs and chips, AI chips require much more computing power, speed, and efficiency. Today’s

AI chips include graphics processing units (GPUs), an application-specific integrated circuit, and

field-programmable gate arrays (FPGAs) [4]. The newer transistors showcase substantial

improvement in running speed and energy efficiency compared to traditional large transistors.

Traditional CPUs lack the processing performance needed while GPUs are capable of handling

parallel processing and can be used in basic AI applications to enhance neural networks. AI

hardware generates an excessive amount of heat, and thus thermal management is key to creating

a cooling system for these high-powered dissipating chips. [5]

The vapor compression evaporation cycle historically repels from electronics because of

the many challenges that could arise, like leakage and connection length. However, it is “one the

most promising alternative cooling techniques for high heat dissipation electronics cooling.” [6]

The vapor compression evaporation system consists of four main components: the evaporator,

the compressor, the condenser, and the expansion valve. The refrigerant leaves the evaporator as

a slightly superheated vapor and enters the compressor. If this path is long, the pressure drops as

a result of fluid friction and heat transfer from the surroundings. As a result, the specific volume

increases causing the compressor to require a higher power input to operate at a steady-flow rate.

The compressor causes the pressure to increase and thus, increases the temperature. The high-pressure, high-temperature refrigerant then enters the condenser to convert the liquid to a

subcooled liquid. This improves cooling capacity and prevents vapor bubbles from entering the

expansion valve. The expansion valve’s throttling effect separates the high and low-pressure

sides of the cycle and decreases saturation temperature. Thus, the refrigerant will boil at a low

temperature in the evaporator. The connecting line between the expansion valve and the

evaporator must be short to avoid decreased pressure [7]. The space allotted in electronics

becomes a challenge when designing cooling systems for chips. Developing a vapor compression

evaporation cycle that is efficient and compact enough to fit in a limited space is an ongoing

challenge [6]. In addition to the bulkiness of the system, liquid and refrigerant systems have

leakage problems [8]. Further work has to be done to integrate liquid or refrigerant cycles into

semiconductors [9]. Our project implements a vapor compression evaporation system utilizing

Refrigerant 134A’s and proper housing unit, power requirements, and arrangements of

components.

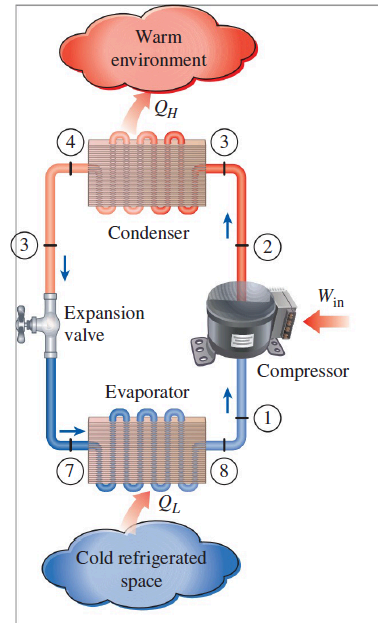
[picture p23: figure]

Diagram of the Vapor-Compression Evaporation Cycle [7]

Literature Survey

There have been plenty of studies and research done to reduce the amount of heat, energy,

and power produced by high-powered chips. With the rise in artificial intelligence (AI), there

will be an even bigger demand for a new thermal design due to the power generated by AI chips

[2]. In analyzing cooling methods to meet these thermal demands, different cooling methods

must be analyzed. Purdue [6] references that Scott [10] classifies electronic cooling techniques,

using refrigeration, into four categories: using refrigerants to cool liquid or air, refrigerating

heatsinks, using liquid nitrogen baths, and thermoelectric cooling. In comparing the refrigeration

of air or liquid technique to the refrigerated heatsink method, Purdue’s [6] general findings are

that using a refrigerated heatsink has a lower temperature at the cold surface. In addition,

because the evaporator would be mounted directly on the electronic component, the electronic

temperature is colder than the surrounding temperature and the refrigerated heatsink method is

more compact than using a cooling fluid. For liquid nitrogen baths, immersion would require a

dewar flask - a container made of insulated material. Special care is required for this method, to

achieve advanced insulation - greater risk of leakage. Lastly, the capacity and overall

effectiveness of the thermoelectric cooling method are minimal and not promising [6]. The first

IBM system to employ refrigeration cooling techniques is the IBM S/390 G4 CMOS server

system. The processing module is the element cooled by refrigeration; its form factor is

267×267×711mm³ and has a weight of 27 kg. To absorb moisture the evaporator contains 260

grams of silica gel. For this G4 server, the average process module temperature was about 40℃

which is 35℃ lower than the air cooling system of the same design. These IBM server units have

been tested and implemented to ensure high reliability [11].

A similar experiment to the one proposed was done by Rajiv Mongia et al. [12], a VCRS

was built to cool down the CPU of a Notebook computer. The working fluid used for this

experiment was Isobutane, also known as R600a. Their refrigeration system consisted of the

following components: An evaporator, a condenser, a throttling device in the form of a capillary

tube, and a compressor. In addition to the components to make up the refrigeration cycle, sensors

were attached at several points throughout the system to measure the temperature and pressure of

each component. The data was recorded using a computerized DAQ system that was

programmed with LabVIEWTM. Several experiments were performed, each time making

modifications to either a component or an operating condition. For example, for some

experiments, the airflow at the condenser was increased or the evaporator (DTTV) power was

decreased. The results of their experiment were evaluated through the coefficient of performance

(COP). They were able to achieve a COP of 2.25 and greater depending on the variables

changed. The highest COP achieved through their experimentation was 3.70 which occurred

when the DTTV power was reduced. A slight increase in COP was also observed when the

airflow at the condenser was increased. Comparing the measured COP and the ideal COP

(Carnot refrigeration system), they reached about 25-30% of the Carnot efficiency, which

increased as the pressure ratio increased. They found that a higher pressure ratio could be

achieved through having a higher gas temperature.

Another solution was evaluated by Lung-Yue Jeng and Tun-Ping Teng [8]; a hybrid

design of a liquid cooling system and a vapor compression refrigeration system (VCRS). To

achieve maximum efficiency a combination of aluminum oxide nanoparticles and water was

used because aluminum oxides disperse easily in water and have good suspension performance.

The liquid coolant was operating at a flow rate of 2.0 L/min. Hydrocarbon refrigerant was used

for the VCRS as it improves the coefficient of performance, cooling capacity, and is

environmentally friendly. To simulate the power of a CPU a heating module made up of “pure

copper blocks were placed in four tubular heaters (150 W x 4DC100V) and placed alongside a

heat exchanger with thermal paste.” Two power supplies were connected to the tubular heaters to

simulate the heat generation. The components that were used for this thermal design were

expansion valve, control valve compressor, pump, condenser, flow meters, and air-cooled heat

exchanger. When compared to the other test methods performed, which include liquid cooling

with distilled water, aluminum oxide, and using VCRS with different types of hydrocarbon

coolants, the hybrid design proved to be the best. It was able to have a cooling capacity of 540

W, a surface temperature of the heater at 75.8℃, and a power consumption of the compressor

and water pump at 29.5 W. The hybrid design also proved to have a cooling capacity 4.5 times

higher than the heat of the CPU.

Some of the changes going to be performed are using an AI chip, R134a refrigerant, and

using a VCRS. . The size of each component will be greater compared to the study done by Rajic

Mongia et al., as the proposed experiment does not hold the same form requirements as the

studied experiment, partially due to the increased power dissipation requirements. The proposed

experiment will also use an expansion valve rather than a capillary tube. Additionally, the

working fluid for this system will be changed to R134a rather than the R600a used. To add to

this the coolant R134a has proved to be an efficient coolant when used in spray cooling and is

considered to be environmentally friendly [13]. We look to implement a vapor compression

refrigeration system as it can be the most suitable for AI chip applications. Its benefits include a low mass flow rate, a high COP, and the ability to transfer heat away from the source with low

cold plate temperatures [6]. To expand upon this refrigeration technique we look to research,

explore, and build a working prototype that uses a refrigerated cooling method in which a heat

sink would operate below ambient temperature - allowing for optimal cooling of high power

dissipating AI chips.

Methodology

After completing the preliminary research and literature review, we will begin designing

a physical model of a system that uses VCRS cooling. This system will include all the major

components of a vapor compression refrigeration system, a cold plate that will be mounted

directly on the component being cooled, as well as a heat exchanger. We intend to build a

prototype that will house the 8 Thermal Test Vehicle (TTV) chips that have identical properties

to that of 8 AI NVIDIA chips, dissipating a power of ~1.1kW each. These TTV chips will be

connected to an external power source to model the heat generated. The end goal will be to have

a working prototype of the system that models the capabilities of refrigeration cooling. We will

use computer-aided design (CAD) software to model our design. We will perform CFD analysis

for thermal and airflow numbers and calculate the system’s overall efficiency and thermal

properties before physically prototyping. We will seek industry knowledge and sponsors to

gather components and gather the necessary funding for our prototype. Once we are able to

build our prototype, we will perform testing on our model. This testing will be done with a DAQ

system that is connected to sensors located throughout various parts of the VCRS: before and

after the compressor, the evaporator (TTV), the condenser, and the expansion valve. We will

make use of transducers and thermocouples to get the pressure and temperature at each location.

This will allow us to determine the heat dissipation of the refrigerant as well as verify that each component of the system behaves as theorized. The testing will be done at multiple levels of

power dissipation leading up to the power dissipation of the 8 AI NVIDIA chips. The COP will

be determined at each of these levels to determine the effects of high heat dissipation on the

system.

Timeline

NUMBER TASK | TASK TITLE | TASK OWNER | START DATE | DUE DATE | DURATION (DAYS)

1 Proposal
1.1 | Introduction | Charlie, Merari Tyler | 9/13/23 9/20/23 | 7
1.1.1 | Literature Review | Marc, Matthew, Waheeb | 9/13/23 9/20/23 | 7
1.2 | Scope | Merari | 9/20/23 9/27/23 | 7
1.3 | Problem Statement Tyler | 9/20/23 9/27/23 | 7
1.4 | Methodology | Marc and
Waheeb 9/20/23 9/27/23 | 7
1.5 | Timeline | Matthew 9/20/23 9/27/23 | 7
1.6 | Outcome | Charlie | 9/20/23 9/27/23 | 7
1.7 | Presentation #1 | Everyone 9/13/23 10/4/23 | 21
2 | Project Oral Presentation #2
2.1 | Initial Design | Marc, Matthew, Merari, Waheeb | 10/4/23 10/18/23 | 14
2.2 | Calculations | Waheeb 10/18/23 10/25/23 | 7
2.2.1 | Engineering
Analysis | Waheeb 10/18/23 10/25/23 | 7
2.3 | Presentation #2 | Everyone 10/4/23 11/1/23 | 27

3

Project Oral
Presentation #3
3.1 | Material Selection Marc | 11/1/23 11/15/23 | 14
3.2 | Part Specification
and Selection

Marc,
Matthew,
Merari,
Waheeb
11/1/23 11/15/23 | 14
3.3 | Purchase Parts | Charlie
and Tyler 11/8/23 11/15/23 | 7
3.4 | Cost Analysis | Charlie
and Tyler 11/8/23 11/15/23 | 7
3.5 | Final Design

Marc,
Matthew,
Merari,
Waheeb
11/15/23 11/22/23 | 7
3.6 | BOM | Charlie
and Tyler 11/15/23 11/22/23 | 7
3.7 | Fabrication Plan | Charlie
and Tyler 11/15/23 11/22/23 | 7
3.8 | Presentation #3 | Everyone 11/1/23 11/29/23 | 28

### 4 Final Report

4.1 | Final Report | Everyone 11/29/23 12/6/23 | 7
4.2 | Individual
Evaluation | Everyone 11/29/23 12/6/23 | 7

Expected Outcome

We expect that refrigeration cooling will be a more effective cooling method than water

cooling for these AI electronic applications. We expect this due to the advantage of operating at a

sub ambient temperature, something water cooling is incapable of. Possible further areas of

research would be to explore various types of refrigerants and compare them against each other.

In addition more testing can be done in a different form factor as well as further investigating

different types of heat exchangers and heat sinks.

Works Cited

[1] Adminxs. (2022, January 31). Is immersion cooling the future of high-performance

computing?. Green Revolution Cooling.

https://www.grcooling.com/blog/immersion-cooling-future-performance-computing/

[2] Ellsworth, M. J., Jr., Goth, G. F., Zoodsma, R. J., Arvelo, A., Campbell, L. A., and Anderl,
W. J. (June 11, 2012). "An Overview of the IBM Power 775 Supercomputer Water Cooling

System." ASME. J. Electron. Package. June 2012; 134(2): 020906.

https://doi.org/10.1115/1.4006140

[3] Jotrin. (2022, January 4). A brief history of the development of Ai Chips. Jotrin Electronics.

https://www.jotrin.com/technology/details/a-brief-history-of-the-development-of-ai-chips

[4] Saif M. Khan and Alexander Mann, "AI Chips: What They Are and Why They Matter"

(Center for Security and Emerging Technology, April 2020),

cset.georgetown.edu/research/ai-chips-what-they-are-and-why-they-matter/.

https://doi.org/10.51593/20190014

https://www.grcooling.com/blog/immersion-cooling-future-performance-computing/https://www

.grcooling.com/blog/immersion-cooling-future-performance-computing/

[5] What is AI chip design? – how it works. Synopsys. (2023).

https://www.synopsys.com/ai/what-is-ai-chip-design.html#:~:text=Traditional%20CPUs%20typi

cally%20lack%20the,be%20applied%20to%20AI%20applications.

[6] Trutassanawin, S., & Groll, E. A. (2004, July). Review of refrigeration technologies for high

heat dissipation. Purdue e-Pubs.

https://docs.lib.purdue.edu/cgi/viewcontent.cgi?article=1677&context=iracc

[7] Çengel, Yunus A., et al. Thermodynamics: An Engineering Approach. McGraw-Hill

Education, 2019.

[8] Jeng, L.-Y., & Teng, T.-P. (2013). Performance evaluation of a hybrid cooling system for

electronic chips. Experimental Thermal and Fluid Science, 45, 155–162.

[9] Blinov, A., Vinnikov, D., & Lehtla, T. (2011). Cooling methods for high-power electronic

systems. Scientific Journal of Riga Technical University. Power and Electrical Engineering,

29(1), 79–86. https://doi.org/10.2478/v10144-011-0014-x

https://doi.org/10.1016/j.expthermflusci.2012.10.020

[10] Scott, A.W., 1974, Cooling of Electronic Equipment, John Wiley and Sons, pp. 204-227.
[11] Schmidt, R.R., and Notohardjono, B.D., 2002, High-End Server Low-Temperature Cooling,

IBM Journal Research and Development, Vol. 46, No. 6, November, pp. 739-751.

[12] Mongia, R., Masahiro, K., DiStefano, E., Barry, J., Chen, W., Izenson, M., Possamai, F.,

Zimmermann, A., & Mochizuki, M. (2006). Small scale refrigeration system for electronics

cooling within a notebook computer. Thermal and Thermomechanical Proceedings 10th

Intersociety Conference on Phenomena in Electronics Systems, 2006. ITHERM 2006.

https://doi.org/10.1109/itherm.2006.1645421

[13] Groulx, D., & Kheirabadi C. A. (2016). Cooling of server electronics: A design review of

existing technology. Applied Thermal Engineering, 105, 622-638.

https://doi.org/10.1016/j.applthermaleng.2016.03.056.

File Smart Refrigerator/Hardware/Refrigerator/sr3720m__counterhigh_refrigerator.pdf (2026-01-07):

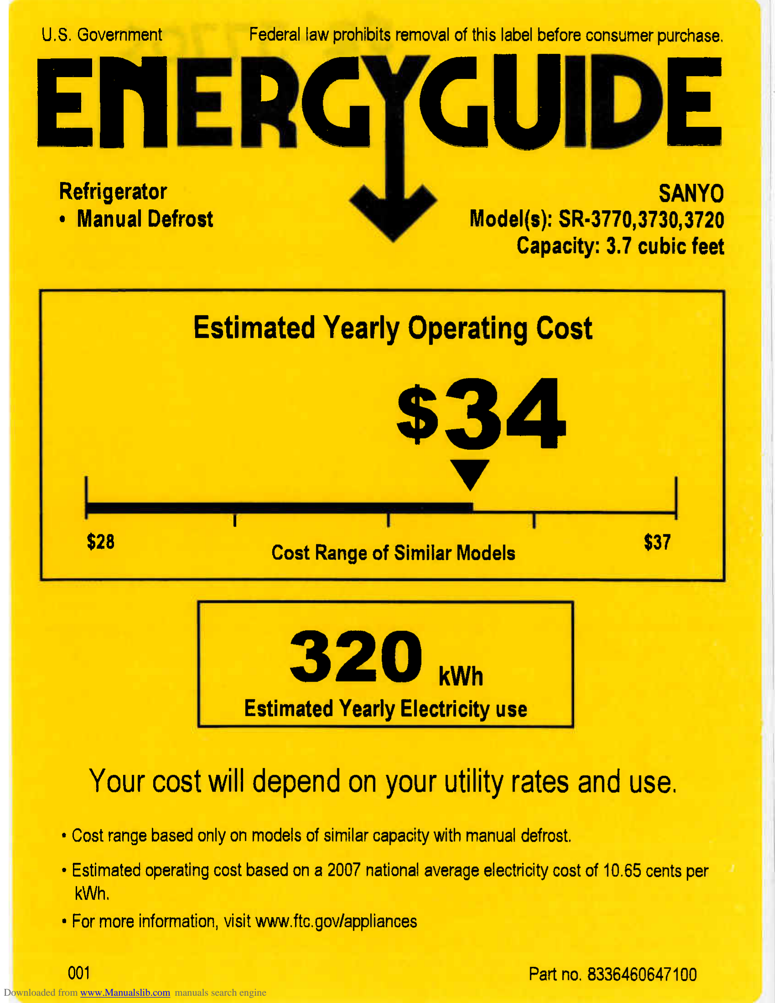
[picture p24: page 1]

Downloaded from www.Manualslib.com manuals search engine

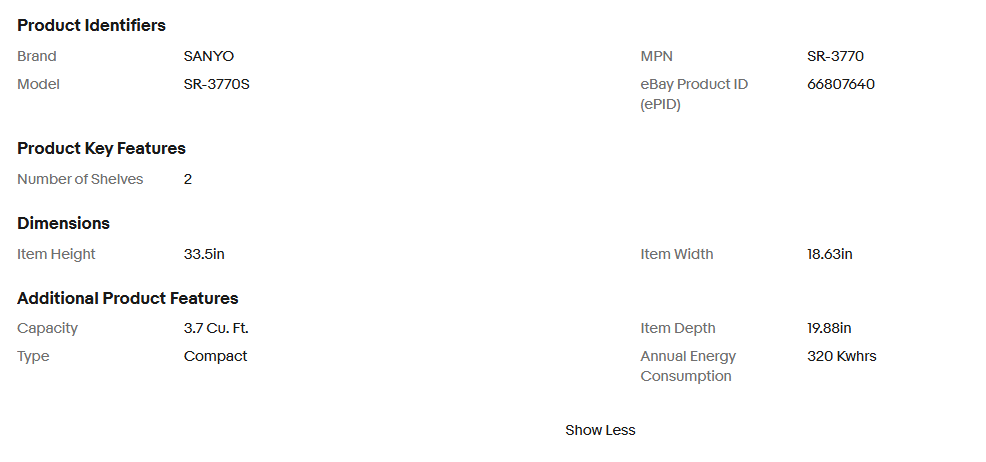
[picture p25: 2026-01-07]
Smart Refrigerator/Hardware/Refrigerator/Size specs.png

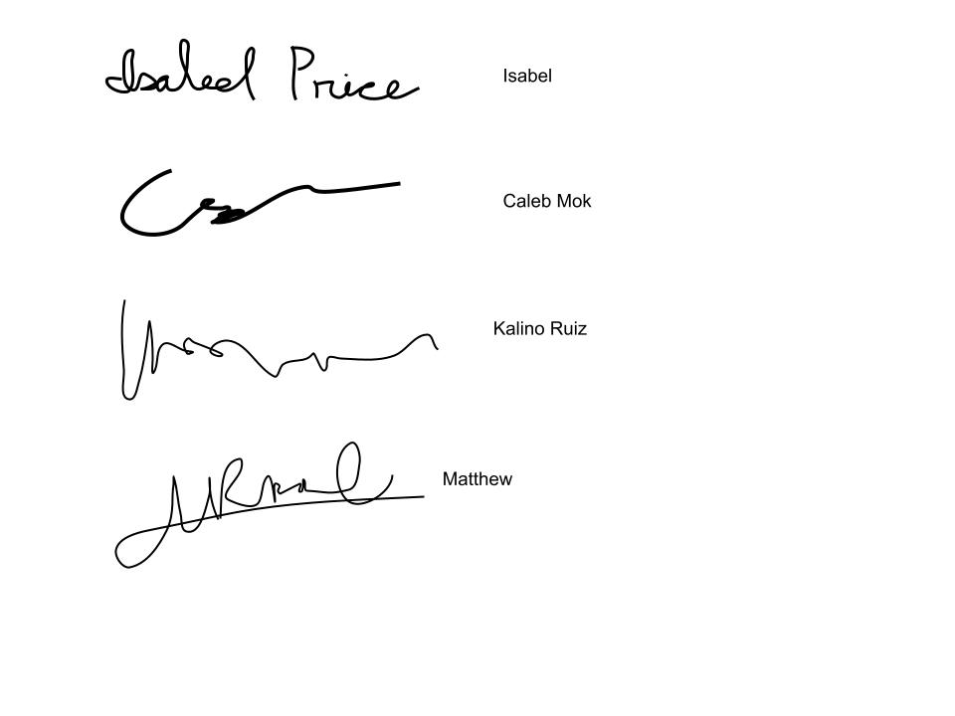
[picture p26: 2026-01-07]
Smart Refrigerator/Misc Assignments/Signatures_.jpg

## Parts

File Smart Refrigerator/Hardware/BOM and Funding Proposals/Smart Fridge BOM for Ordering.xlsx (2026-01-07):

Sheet: Sheet1
Project Name | Smart Refrigerator
Advisor | Dr. Keith Yi
Team Members
Name | Email
Isabel Price | isabel.price@sjsu.edu
Kalino Ruiz | kalino.ruiz@sjsu.edu
Brent Marin | brent.marin@sjsu.edu
Caleb Mok | caleb.mok@sjsu.edu
Matthew Manuel | matthew.manuel@sjsu.edu
Items Requested | Vendor | Qty | Unit Cost | Ext. Cost | Estimated Shipping + tax | Total Per Vendor | Notes
https://www.amazon.com/FANOVO-Refrigerator-Recharge-Refrigerant-Self-Sealing/dp/B09S69H5DP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 | Amazon | 1 | $20.99 | $20.99 | $4.75 | $47.52
https://www.amazon.com/GOORY-Copper-Tubing-0-328-Refrigeration/dp/B0DKT3JDPT | Amazon | 1 | $16.59 | $16.59 |  |  | If $459 is too much over budget, Please remove this item!
https://www.amazon.com/ER2188820-ERP-Thermistor-Replaces-2188820/dp/B01M8OFHHX | Amazon | 2 | $4.97 | $9.94 |  |  | Currently on sale for $5
https://coldhose.com/products/r134a-refrigerant-12oz-can?variant=35532320014496 | Cold Hose | 1 | $14.00 | $14.00 | $11.32 | $25.32
https://www.metalsdepot.com/aluminum-products/aluminum-rectangle-tube?product=290 | Metals Depot | 12 | $11.08 | $132.96 | $19.58 | $243.34 | Please See Section A Below
https://www.metalsdepot.com/aluminum-products/aluminum-sheet?product=381 | Metals Depot | 2 | $45.40 | $90.80 |  |  | Please See Section B Below
https://heatsinkonline.com/products/7874-wide-heatsink-64as?variant=42105916653730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 | Heat Sink | 8 | $11.39 | $91.12 | $21.42 | $112.54 | Please See Section C Below
https://www.jameco.com/z/SP100A-1123XBT-GN-Sunon-120mm-115-VAC-60Hz-Ball-Bearing-Fan-240mA-20W-117-CFM_102884.html | JameCo Electronics | 1 | $13.95 | $13.95 | $12.50 | $30.40
https://www.jameco.com/z/TM1637-JVP-Jameco-ValuePro-TM1637-4-Bits-Digital-Red-LED-Display-Module-for-Arduino-7-Segment-0-36-4-Digit-Clock-Anode-Serial-Driver-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 | JameCo Electronics | 1 | $3.95 | $3.95 |  |  | Included in shipping is $2.09 Tariff Surcharge
 |  |  |  |  | Total Cost | $459.12
Section A
STEP 1 - Select Size Dropdown. Part Number: T34118. The link should automatically bring you to this part
STEP 2 - Select Cut to Size
STEP 2 - Quantity = 12, 6 inches each
Section B
STEP 1 - Select Size Dropdown. Part Number: S3063. The link should automatically bring you to this part
STEP 2 - Select 2 Ft x 2 Ft. Quantity = 2
Example of Completed MetalsDepot Shopping Cart
Section C
Please choose 6 inches length, quantity 8

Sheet: BOM for Presentation 1
Project Name |  | Smart Refrigerator
Advisor |  | Dr. Keith Yi
Team Members
Name |  | Email
Isabel Price |  | isabel.price@sjsu.edu
Kalino Ruiz |  | kalino.ruiz@sjsu.edu
Brent Marin |  | brent.marin@sjsu.edu
Caleb Mok |  | caleb.mok@sjsu.edu
Matthew Manuel |  | matthew.manuel@sjsu.edu
Link | Item | Vendor | Qty | Unit Cost | Estimated Shipping + tax | Total Per Vendor
https://www.amazon.com/BOJACK-DS18B20-Temperature-Stainless-Waterproof/dp/B09NVFJYPS?s=industrial | Temperature Sensor (2 Pack) | Amazon | 1 | $5.99 | $3.54 | $38.88
https://www.amazon.com/dp/B00LW15A4W?ref=ppx_pop_mob_ap_share&th=1 | One Channel Relays (2 Pack) | Amazon | 1 | $7.39
https://www.amazon.com/dp/B093GW6SZ1?ref=ppx_pop_mob_ap_share | AC to DC Converter (5 Pack) | Amazon | 1 | $9.99
https://www.amazon.com/dp/B0FGJ7N5JG?titleSource=true | 3 Way Wire Splitters (10 Pack) | Amazon | 1 | $5.99
https://www.amazon.com/dp/B0F4P352BB?ref=ppx_pop_mob_ap_share | Resistors | Amazon | 1 | $5.99
https://www.metalsdepot.com/aluminum-products/aluminum-sheet?product=381 | Aluminum Sheets | Metals Depot | 2 | $45.40 | $19.58 | $110.38
https://heatsinkonline.com/products/7874-wide-heatsink-64as?variant=42105916653730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 | Heat Sink | Heat Sink Online | 8 | $11.39 | $21.42 | $112.54
https://www.jameco.com/z/SP100A-1123XBT-GN-Sunon-120mm-115-VAC-60Hz-Ball-Bearing-Fan-240mA-20W-117-CFM_102884.html | Fan | JameCo Electronics | 1 | $13.95 | $12.50 | $30.40
https://www.jameco.com/z/TM1637-JVP-Jameco-ValuePro-TM1637-4-Bits-Digital-Red-LED-Display-Module-for-Arduino-7-Segment-0-36-4-Digit-Clock-Anode-Serial-Driver-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 | 4 Digit Display | JameCo Electronics | 1 | $3.95
Already owned | Buttons | Already owned | 5 | - | - | -
Already owned | LED | Already owned | 2 | - | - | -
Already owned | Breadboard | Already owned | 1 | - | - | -
Already owned | Buck Converter | Already owned | 1 | - | - | -
https://www.homedepot.com/p/Loctite-Silicone-Waterproof-Multipurpose-Adhesive-Sealant-2-7-oz-Clear-Tube-908570/303769575 | SIlicone Waterproof Sealant | Home Depot | 1 | $6.28 | $0.63 | $6.91
https://www.amazon.com/Antrader-2-54mm-Sockets-Female-Connector/dp/B0BVHMTY5S?s=industrial | IDC Female Cable Connector | Amazon | 1 | $5.99 | $0.00 | $27.66
https://www.amazon.com/Antrader-Ribbon-Cable-2-54mm-Connectors/dp/B07P77YRB2 | Ribbon Cable | Amazon | 1 | $8.49
https://www.amazon.com/dp/B0D12GZLL9?titleSource=true | DIY Solder Board Kit | Amazon | 1 | $7.59
https://www.amazon.com/dp/B07Q7NZTQS?titleSource=true | Clock Memory Module (2 pack) | Amazon | 1 | $5.59
 |  |  |  |  | Total Cost | $326.77

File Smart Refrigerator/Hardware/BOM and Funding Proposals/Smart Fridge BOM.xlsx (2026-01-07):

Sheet: Sheet1
Component Name | MFG# | Description/Purpose | Quantity | Cost/Unit | Shipping | Total | Notes | Link | 0
Fan | SP100A | 4.68 Inch AC Tube Axial | 1 | 13.95 | $9.18 | $23.13 | Meets CFM requirement | https://www.jameco.com/z/SP100A-1123XBT-GN-Sunon-120mm-115-VAC-60Hz-Ball-Bearing-Fan-240mA-20W-117-CFM_102884.html | 0
Piping Disconnect Kit | B09S69H5DP | To pressurize and add pipe lenght | 1 | 20.99 | $0.00 | $20.99 | Will need can of R-134a | https://www.amazon.com/FANOVO-Refrigerator-Recharge-Refrigerant-Self-Sealing/dp/B09S69H5DP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 | 0
Copper Pipe | 630456606893 | Refrigerant Piping 3/8" OD | 1 | 16.99 | $0.00 | $16.99 | 5 Feet of tubing | https://www.amazon.com/GOORY-Copper-Tubing-0-328-Refrigeration/dp/B0DKT3JDPT | 0
R-134A | SER134A | Pure R-134A | 1 | 14.00 | $11.32 | $25.32 |  | https://coldhose.com/products/r134a-refrigerant-12oz-can?variant=35532320014496 | 0
Heatsink | 64AS | 7.874'' (200mm) Wide Heatsink (64AS) | 8 | 9.90 | $12.36 | $91.56 | 7.9" x 6" | https://heatsinkonline.com/products/7874-wide-heatsink-64as?variant=42105916653730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 | 0
Temperature Sensor | ERP 2188820 | Refrigerator Thermistor | 2 | 11.00 | $0.00 | $22.00 | regulate temperature | https://www.amazon.com/ER2188820-ERP-Thermistor-Replaces-2188820/dp/B01M8OFHHX | 0
Display | TM1637 | 4 Digit 7 Segment Display | 1 | 3.95 | $4.09 | $8.04 | Check if compatible with microcontroller | https://www.jameco.com/z/TM1637-JVP-Jameco-ValuePro-TM1637-4-Bits-Digital-Red-LED-Display-Module-for-Arduino-7-Segment-0-36-4-Digit-Clock-Anode-Serial-Driver-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 | 0
Buttons | EK1019 | 6x6x4.3mm TACT Switch Push Button | 1 | 6.98 | $0.00 | $6.98 | (pack of 50) | https://www.amazon.com/Gikfun-6x6x5mm-Switch-Button-Arduino/dp/B00R17XUFC?gQT=2 | 0
Aluminum Tube | T34118 | Ice casings | 12 | 9.30 | $41.00 | $152.60 | 4x1x1/8"x6 | https://www.metalsdepot.com/aluminum-products/aluminum-rectangle-tube | 0
Sheet Aluminum | S3063 | Ice Casings | 2 | 42.72 |  | $85.44 | 24"x24"x1/16" | https://www.metalsdepot.com/aluminum-products/aluminum-sheet | 0
Microcontroller | ESP32 | Control the Fridge | 1 | 8.00 | $0.00 | $8.00 | have already | https://www.espressif.com/en/products/socs/esp32 | 0
 |  |  |  | TOTAL: |  | $461.05
 |  |  |  |  |  | $446.07
 |  |  |  |  |  |  | 647.75
Stuff just for reference
VFD | WCI 5304531506 | Inverter | 1 | 102.20 |  | $102.20 |  | https://www.reliableparts.com/wci-5304531506.html
Mini Fridge | SNFSR3770S | Have on hand already | 1 | 0.00 |  | $0.00 | Is not currently working
Mini Fridge | SNFSR3770S | Possible Replacement | 1 | 150.00 |  | $150.00 | possible replacemnt off of Craigslist or marketplace
Grated Shelves |  |  |  |  |  | $0.00
Thermal Fuse | ERP DA47-00095E | Refrigerator Thermal Fuse | 1 | 12.05 |  | $12.05 |  | https://www.amazon.com/ERP-Fuse-Thermal-DA47-00095E/dp/B01MG8RAZP
Defrost Heater | AMI PARTS WR51X10055 | Refrigerator Defrost Heater Kit | 1 | 16.77 |  | $16.77 |  | https://www.amazon.com/Refrigerator-WR51X10055-Temperature-WR55X10025-Replacement/dp/B07TP267QR
Defrost Sensor | ERP 6615JB2005H | Refrigerator Defrost Sensor | 1 | 12.95 |  | $12.95 |  | https://www.amazon.com/ERP-Refrigerator-AP4438477-PS3529340-6615JB2005H/dp/B07BZJ87RC?gQT=1
Reed Switch | CPS-500 | Reed Switch Sensor Switch | 1 | 22.19 |  | $22.19 |  | https://www.amazon.com/ZMYXMDM-Magnetic-Control-Universal-Refrigerator/dp/B0DCYWYYF7?gQT=1
Relay Module |  |  | 1 | 6.99 |  | $6.99 |  | https://www.amazon.com/AEDIKO-Channel-Optocoupler-Isolation-Support/dp/B095YFJ69T?gQT=1
Compressor | C-QN43L2A | Replacement Compressor | 1 | 105.99 | $0.00 | $105.99 | To fix fridge | https://www.ebay.com/itm/205193409371 | 0
 |  |  |  |  |  | $0.00
 |  |  |  |  |  | $0.00
 |  |  |  |  |  | $0.00
 |  |  |  |  |  | $0.00
 |  |  |  |  |  | $0.00
The defrost mechanism ensures frost won’t build up around the evaporator coils. It consists of a defrost thermistor that will detect the buildup of frost, a defrost heater that will heat up the surrounding evaporator coils to remove it, and a thermal fuse as a safety precaution that will shut down the heater if it gets too hot. Lastly, there is the reed switch that will turn on the LEDs when the door is opened. |  |  |  |  |  | $0.00
 |  |  |  |  |  | $0.00
 |  |  |  |  |  | $0.00
 |  |  |  |  |  | $0.00
 |  |  |  |  |  | $0.00
 |  |  |  |  |  | $0.00
 |  |  |  |  |  | $0.00
 |  |  |  |  |  | $0.00
 |  |  |  |  |  | $0.00
 |  |  |  |  |  | $0.00

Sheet: Last Electronics To Purchase
https://www.amazon.com/HiLetgo-Channel-optocoupler-Support-Trigger/dp/B00LW15A4W?s=industrial | Relay
https://www.amazon.com/Acxico-700mA-Module-Converter-Supply/dp/B093GW6SZ1 | Power Converter
https://www.amazon.com/QTETAK-Momentary-Tactile-Button-Assortment/dp/B0BFWK5N8V?sp_csd=d2lkZ2V0TmFtZT1zcF9hdGY | Buttons
https://www.amazon.com/Connector-Splitter-Splicing-Terminal-Connectors/dp/B0FGJ7N5JG?s=industrial | 1 in 3 out Splitter
https://www.amazon.com/EP-Appliance-Replacement-Supply-Pigtail/dp/B0CLCPD8X6?sp_csd=d2lkZ2V0TmFtZT1zcF9tdGY | AC power supply

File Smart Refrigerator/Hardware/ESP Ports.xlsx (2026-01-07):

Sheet: Datasheets
Component | Description | Datasheet | Power | Resources | Libraries
TM1637 | 7-Segment |  | 5V | https://www.hackster.io/ryanchan/tm1637-digit-display-arduino-quick-tutorial-ca8a93 | TM1637 by AVISHAY ORPAZ | TM1637 Grove 4digit display by seeeed
DS18B20 | Temp Sensor | https://www.analog.com/media/en/technical-documentation/data-sheets/ds18b20.pdf | 5V | https://randomnerdtutorials.com/guide-for-ds18b20-temperature-sensor-with-arduino/ | OneWire by Jim Studt | DallasTemperature by Miles Burton
Relay |  |  |  | https://lastminuteengineers.com/one-channel-relay-module-arduino-tutorial/
AC to DC |  |  |  | https://www.amazon.de/-/en/Acxico-700mA-Module-Converter-Supply/dp/B093GW6SZ1
Fan
Buck

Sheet: Pin Diagram - PCB NEW 121
 |  |  | GND
 |  | BUTTON | OUT - 7 Segment (DIO)
NO |  |  | OUT - 7 Segment (CLK)
NO |  |  | NO
NO |  |  | NO
NO |  |  | MEMORY MODULE
OUT-LED
OUT-LED |  |  | BUTTON
 |  |  | MEMORY MODULE
OUT - Compressor Relay
OUT - Fan Relay
BUTTON |  |  | IN - Temp Sensor
 |  |  | BUTTON
 |  |  | NO
BUTTON |  |  | Button
NO
NO |  |  | NO
NO |  |  | NO
5 |  |  | 8
Clockset 27 --> 2
Out - Compressor Relay --> 2 to 26
OUut - Fan Relay 15 --> 27
 | 38

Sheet: Pin Diagram - PCB OLD 1130
 |  | GND
 | BUTTON | OUT - 7 Segment (DIO)
NO |  | OUT - 7 Segment (CLK)
NO |  | NO
NO |  | NO
NO |  | MEMORY MODULE
OUT-LED
OUT-LED |  | BUTTON
 |  | MEMORY MODULE
BUTTON
BUTTON |  | IN - Temp Sensor
 |  | BUTTON
 |  | NO
BUTTON |  | OUT - Compressor Relay
NO |  | OUT - Fan Relay
NO |  | NO
NO |  | NO
5 |  | 8

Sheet: Pin Diagram - PCB old
3.3
In - Clock Set Button
In - Start Pass Button
IN - End Pass Button
IN - Hour Button | OUT - 7 Segment (CLK)
 | OUT - 7 Segment (DIO)
IN - Minute Button
OUT - Passive LED
 | IN - Temp Sensor
OUT - Active LED | OUT - Compressor Relay
NO | OUT - Fan Relay
NO
NO
5

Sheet: Pin Diagram - Prototype
LED - Passive
LED - Active
Button - Clockset
Button - Passive End
Button - Passive Start
Button - Minute | OUT - 7 Segment (CLK)
Button - Hour | OUT - 7 Segment (DIO)
 | IN - Temp Sensor
 | OUT - Compressor Relay
 | OUT - Fan Relay

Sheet: Good v Bad Pins
GPIO | Input | Output | Using Input or Output? | Connected to | Notes
0 | pulled up | OK |  |  | outputs PWM signal at boot, must be LOW to enter flashing mode
1 | TX pin | OK |  |  | debug output at boot
2 | OK | OK | Output | Compressor Relay | connected to on-board LED, must be left floating or LOW to enter flashing mode
3 | OK | RX pin |  |  | HIGH at boot
4 | OK | OK
5 | OK | OK |  |  | outputs PWM signal at boot, strapping pin
6 | x | x |  |  | connected to the integrated SPI flash
7 | x | x |  |  | connected to the integrated SPI flash
8 | x | x |  |  | connected to the integrated SPI flash
9 | x | x |  |  | connected to the integrated SPI flash
10 | x | x |  |  | connected to the integrated SPI flash
11 | x | x |  |  | connected to the integrated SPI flash
12 | OK | OK |  |  | boot fails if pulled high, strapping pin
13 | OK | OK
14 | OK | OK |  |  | outputs PWM signal at boot
15 | OK | OK | OUTPUT | Fan relay | outputs PWM signal at boot, strapping pin
16 | OK | OK | INPUT - Sensor | Temp sensor
17 | OK | OK
18 | OK | OK | Output - 7 Segment | DIO
19 | OK | OK | Output - 7 Segment | CLK
21 | OK | OK
22 | OK | OK
23 | OK | OK
25 | OK | OK | OUTPUT - LED | ACTIVE
26 | OK | OK
27 | OK | OK
32 | OK | OK | Input - Button | MINUTE
33 | OK | OK | OUTPUT - LED | PASSIVE
34 | OK |  | Input - Button | END PASS | input only
35 | OK |  | Input - Button | HOUR | input only
36 | OK |  | Input - Button | CLOCK SET | input only
39 | OK |  | Input - Button | START PASS | input only

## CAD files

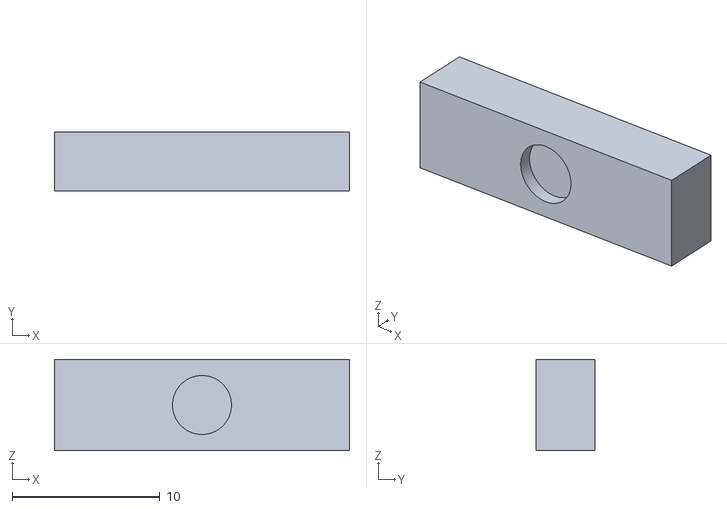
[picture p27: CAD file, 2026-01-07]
Smart Refrigerator/CAD models/the button of doom.stl
20.0 x 4.00 x 6.20

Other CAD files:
Smart Refrigerator/CAD models/3d printed walls.f3d
Smart Refrigerator/CAD models/Button(s) ignore the tiny ones idk how to export just one button to f3d.f3d

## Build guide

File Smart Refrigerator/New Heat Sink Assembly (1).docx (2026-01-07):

~3/8"

1/16"

5/16"

.25"

13.75"

Total Space to work with: 14.25

Pull the corners of the bags through those slots. Lock somehow.

0.5"

0.787"

4.⁷

SLOT FOR BAG CORNER

Plastic Bag full of water/ice. Calc water needed per layer using the percentage caleb found a few weeks ago

MAX: 13.75" 13.75 - 7.874 = 5.876 " = 5 7/8"

0'-5 13/16"

0'-5/16"

0'-7 7/8"

m

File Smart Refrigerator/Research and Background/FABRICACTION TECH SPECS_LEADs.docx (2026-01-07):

Fabrication:

- pull existing refrigeration cycle out
- Mount on back of refrigerator
- Replace piping as an air channel (almost like a plenum)

Fabrication Resources:

- Ryan D’amour, DMG North, Kegerator
  - Built a device using a refrigeration cycle to keep a keg cool
- Tyler Yang, SJSU Alumni, Senior Design project
  - Senior project was an active refrigeration cycle to keep PC chips cool

Industry Connections:

- RAE Coils
- Danfoss (Expansion Valves)

Vendors for parts/supplies:

- Grainger Industrial Supply
- Supply House

For Piping:
We need the following info”
Refrigerant flow required

Diameter

Lengths

insulated/uninsulated

Static pressure

Piping connections

Quick connect valve $15-$50

Fan Options:
Need airflow (cfm)

Could use a CPU fan or smt of the sort, quiet, compact and easy to control

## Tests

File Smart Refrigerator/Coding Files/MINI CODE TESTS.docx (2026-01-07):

+’-LIBRARIES TO ADD:

TM1637 by AVISHAY ORPAZ

OneWire by Jim Studt

DallasTemperature by Miles Burton

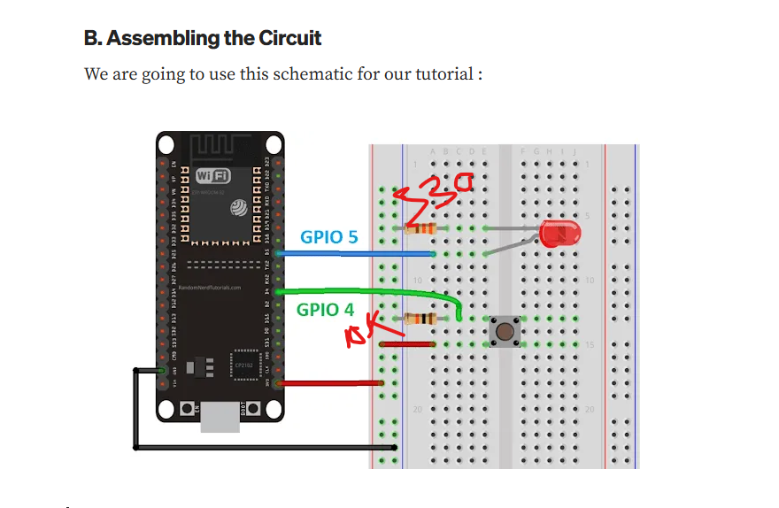
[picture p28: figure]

// set pin numbers

const int buttonPin = 4; // the number of the pushbutton pin

const int ledPin = 5; // the number of the LED pin

// variable for storing the pushbutton status

int buttonState = 0;

void setup() {

Serial.begin(115200);

// initialize the pushbutton pin as an input

pinMode(buttonPin, INPUT);

// initialize the LED pin as an output

pinMode(ledPin, OUTPUT);

}

void loop() {

// read the state of the pushbutton value

buttonState = digitalRead(buttonPin);

Serial.println(buttonState);

// check if the pushbutton is pressed.

// if it is, the buttonState is HIGH

if (buttonState == HIGH) {

// turn LED on

digitalWrite(ledPin, HIGH);

}

else {

// turn LED off

digitalWrite(ledPin, LOW);}

}

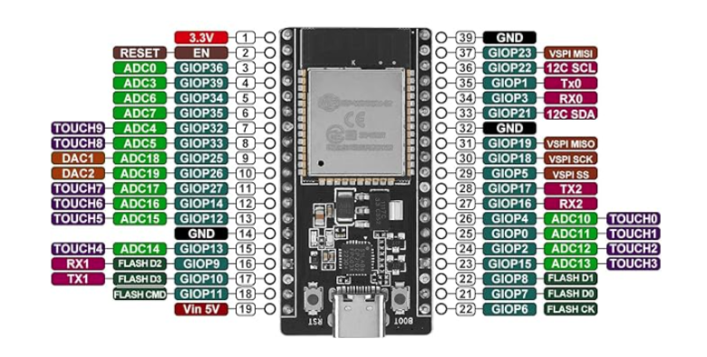
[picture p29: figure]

#include <TM1637Display.h>

// Define the CLK and DIO pins connected to the TM1637 display

#define CLK_PIN 2

#define DIO_PIN 4

// Create a display object

TM1637Display display(CLK_PIN, DIO_PIN);

void setup() {

Serial.begin(115200);

display.setBrightness(0x0f); // Set brightness to maximum (0x00 - 0x0f)

}

void loop() {

// Display a number

display.showNumberDec(1234);

delay(2000);

// Display a number with leading zeros

display.showNumberDec(5, true); // Displays 0005

delay(2000);

// Display a number with colon

display.showNumberDecEx(1530, 0b01000000, false, 4, 0); // Displays 15.30 (colon at the second position)

delay(2000);

// Display segments directly (e.g., "TEST")

uint8_t data[] = {

display.encodeDigit(10), // T

display.encodeDigit(14), // E

display.encodeDigit(12), // S

display.encodeDigit(10) // T

};

display.setSegments(data);

delay(2000);

// Clear the display

display.clear();

delay(1000);

}

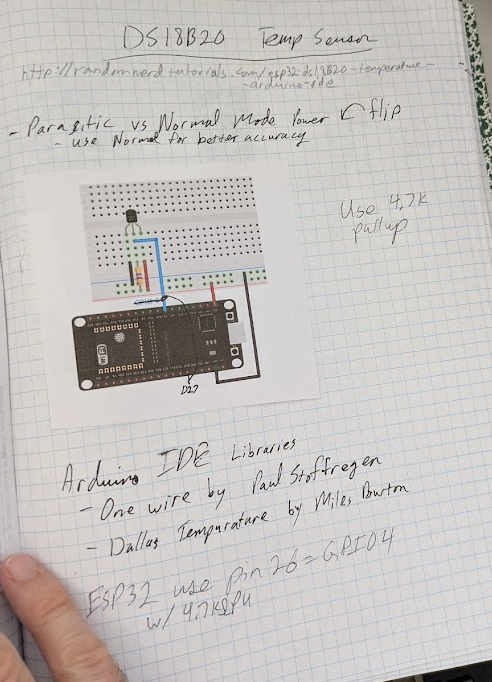
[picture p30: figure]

https://randomnerdtutorials.com/guide-for-ds18b20-temperature-sensor-with-arduino/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,Temperature%20library%20by%20Miles%20Burton.

https://www.hackster.io/ryanchan/tm1637-digit-display-arduino-quick-tutorial-ca8a93

https://randomnerdtutorials.com/guide-for-ds18b20-temperature-sensor-with-arduino/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,Temperature%20library%20by%20Miles%20Burton

https://lastminuteengineers.com/one-channel-relay-module-arduino-tutorial/

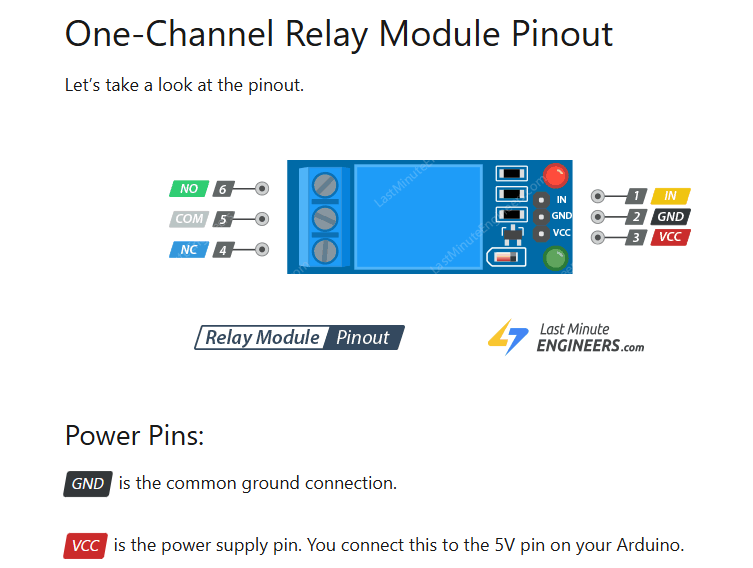
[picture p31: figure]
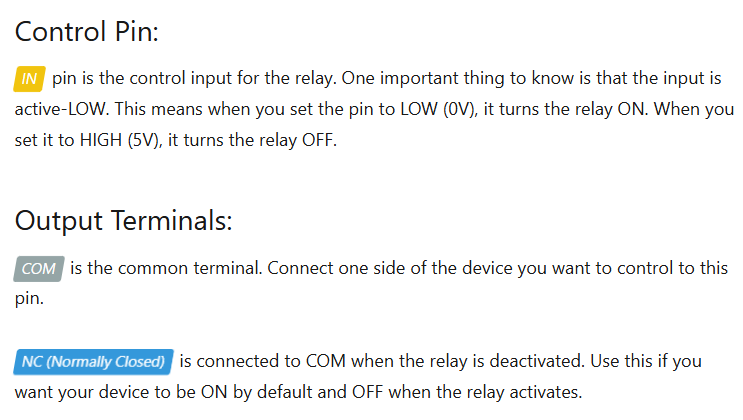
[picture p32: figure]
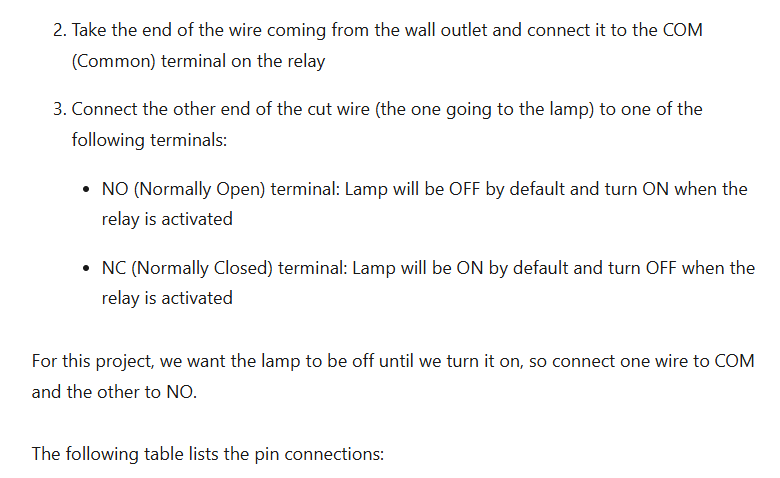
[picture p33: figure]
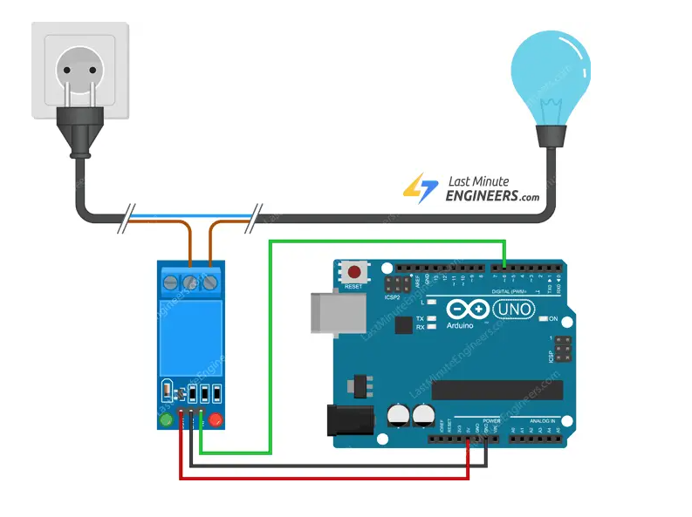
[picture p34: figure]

int RelayPin = 6;

void setup() {

// Set RelayPin as an output pin

pinMode(RelayPin, OUTPUT);

}

void loop() {

// Let's turn on the relay...

digitalWrite(RelayPin, LOW);

delay(3000);

// Let's turn off the relay...

digitalWrite(RelayPin, HIGH);

delay(3000);

}

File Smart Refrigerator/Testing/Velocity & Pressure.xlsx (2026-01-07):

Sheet: RAW DATA
Without Vein
TOP | 100 | 845 | 710 | 492 | 52 | 70 | 80 | 55 | 20 | 62 | 160
 | 110 | 735 | 640 | 470 | 45 | 70 | 50 | 33 | 33 | 60 | 162
MIDDLE | 680 | 80 | 50 | 50 | 106 | 50 | 47 | 20 | 60 | 10 | 57
 | 780 | 82 | 57 | 56 | 128 | 30 | 65 | 30 | 26 | 90 | 47
BOTTOM | 100 | 950 | 970 | 390 | 124 | 36 | 11 | 35 | 152 | 275 | 365
 | 168 | 1186 | 1021 | 401 | 148 | 50 | 13 | 32 | 139 | 277 | 341
With Vein
TOP | 613 | 668 | 727 | 558 | 210 | 33 | 57 | 47 | 19 | 76 | 44
 | 541 | 617 | 667 | 507 | 141 | 33 | 49 | 30.5 | 17 | 72 | 43
BOTTOM | 483 | 873 | 71 | 9 | 5 | 32 | 11 | 3.5 | 39 | 151 | 158
 | 456 | 926 | 67 | 21 | 24 | 35 | 6 | 5 | 31 | 133 | 181
RETURN | 445 | 35 | 34 | 1
PRESSURE | INLET | OUTLET
inH2O | 0.05 | -0.16
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

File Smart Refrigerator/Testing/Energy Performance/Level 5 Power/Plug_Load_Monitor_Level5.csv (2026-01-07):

Plot Title: Plug Load Monitor
# | Date Time, GMT-07:00 | RMS Voltage, V (LGR S/N: 10758121, SEN S/N: 10758121, LBL: RMSVoltageV) | RMS Voltage - Max, V (LGR S/N: 10758121, SEN S/N: 10758121, LBL: RMSVoltageV) | RMS Voltage - Min, V (LGR S/N: 10758121, SEN S/N: 10758121, LBL: RMSVoltageV) | RMS Voltage - Avg, V (LGR S/N: 10758121, SEN S/N: 10758121, LBL: RMSVoltageV) | RMS Current, A (LGR S/N: 10758121, SEN S/N: 10758121, LBL: RMSCurrentA) | RMS Current - Max, A (LGR S/N: 10758121, SEN S/N: 10758121, LBL: RMSCurrentA) | RMS Current - Min, A (LGR S/N: 10758121, SEN S/N: 10758121, LBL: RMSCurrentA) | Active Power, W (LGR S/N: 10758121, SEN S/N: 10758121, LBL: ActivePowerW) | Active Energy, Wh (LGR S/N: 10758121, SEN S/N: 10758121, LBL: ActiveEnergyWh) | Apparent Power, VA (LGR S/N: 10758121, SEN S/N: 10758121, LBL: ApparentPowerVA) | Power Factor, PF (LGR S/N: 10758121, SEN S/N: 10758121, LBL: PowerFactorPF) | Line Resume (LGR S/N: 10758121) | Line Loss (LGR S/N: 10758121) | Stopped (LGR S/N: 10758121) | End Of File (LGR S/N: 10758121)
1 | 09/09/25 09:00:23 PM | 0.00 | 0.00 | 0.00 | 0.00 | 0.0000 | 0.0000 | 0.0000 | 0.00 | 0.00000000 | 0.00 | 0.00
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

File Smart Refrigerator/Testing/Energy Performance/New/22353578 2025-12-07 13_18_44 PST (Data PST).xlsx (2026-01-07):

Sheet: Data
# | Date-Time (PST) | Temperature , °C | RH , % | Dew Point , °C
1 | 2025-11-25 17:21 | 17.87 | 55.85 | 8.95
2 | 2025-11-25 17:22 | 18.11 | 57.15 | 9.51
3 | 2025-11-25 17:23 | 18.41 | 55.66 | 9.40
4 | 2025-11-25 17:24 | 19.22 | 55.63 | 10.15
5 | 2025-11-25 17:25 | 19.62 | 48.59 | 8.50
6 | 2025-11-25 17:26 | 19.47 | 49.82 | 8.74
7 | 2025-11-25 17:27 | 19.20 | 52.96 | 9.39
8 | 2025-11-25 17:28 | 18.92 | 51.92 | 8.84
9 | 2025-11-25 17:29 | 18.72 | 53.40 | 9.07
10 | 2025-11-25 17:30 | 18.55 | 52.76 | 8.74
11 | 2025-11-25 17:31 | 18.43 | 53.50 | 8.83
12 | 2025-11-25 17:32 | 18.33 | 54.34 | 8.97
13 | 2025-11-25 17:33 | 18.26 | 54.80 | 9.03
14 | 2025-11-25 17:34 | 18.22 | 54.83 | 9.00
15 | 2025-11-25 17:35 | 18.17 | 55.05 | 9.01
16 | 2025-11-25 17:36 | 18.15 | 54.82 | 8.93
17 | 2025-11-25 17:37 | 18.14 | 55.06 | 8.99
18 | 2025-11-25 17:38 | 18.15 | 55.44 | 9.10
19 | 2025-11-25 17:39 | 18.16 | 55.34 | 9.08
20 | 2025-11-25 17:40 | 18.20 | 55.35 | 9.12
21 | 2025-11-25 17:41 | 18.22 | 55.13 | 9.09
22 | 2025-11-25 17:42 | 18.24 | 55.80 | 9.28
23 | 2025-11-25 17:43 | 18.27 | 54.94 | 9.08
24 | 2025-11-25 17:44 | 18.30 | 54.74 | 9.05
25 | 2025-11-25 17:45 | 18.32 | 54.70 | 9.06
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

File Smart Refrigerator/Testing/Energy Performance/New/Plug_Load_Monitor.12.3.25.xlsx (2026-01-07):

Plot Title: Plug Load Monitor
# | Date Time, GMT-08:00 | RMS Voltage, V (LGR S/N: 10758121, SEN S/N: 10758121, LBL: RMSVoltageV) | RMS Current, A (LGR S/N: 10758121, SEN S/N: 10758121, LBL: RMSCurrentA) | Active Power, W (LGR S/N: 10758121, SEN S/N: 10758121, LBL: ActivePowerW) | Active Energy, Wh (LGR S/N: 10758121, SEN S/N: 10758121, LBL: ActiveEnergyWh) | Apparent Power, VA (LGR S/N: 10758121, SEN S/N: 10758121, LBL: ApparentPowerVA) | Power Factor, PF (LGR S/N: 10758121, SEN S/N: 10758121, LBL: PowerFactorPF) | Host Connected (LGR S/N: 10758121) | Line Loss (LGR S/N: 10758121) | Line Resume (LGR S/N: 10758121) | End Of File (LGR S/N: 10758121)
1 | 2025-11-28 16:12 | 120.66 | 0.8296 | 71.75 | 0 | 100.09 | 0.72
2 | 2025-11-28 16:13 | 120.72 | 0.8214 | 70.48 | 1.18398595 | 99.15 | 0.71
3 | 2025-11-28 16:14 | 120.68 | 0.8143 | 69.4 | 1.16520405 | 98.26 | 0.71
4 | 2025-11-28 16:15 | 120.54 | 0.8073 | 68.36 | 1.14747214 | 97.3 | 0.7
5 | 2025-11-28 16:16 | 120.66 | 0.8006 | 67.34 | 1.13241625 | 96.59 | 0.7
6 | 2025-11-28 16:17 | 120.7 | 0.794 | 66.28 | 1.11088026 | 95.82 | 0.69
7 | 2025-11-28 16:18 | 120.55 | 0.7894 | 65.61 | 1.09837186 | 95.14 | 0.69
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

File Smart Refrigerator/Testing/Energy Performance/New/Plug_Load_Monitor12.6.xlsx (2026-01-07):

Plot Title: Plug Load Monitor
# | Date Time, GMT-08:00 | RMS Voltage, V (LGR S/N: 10758121, SEN S/N: 10758121, LBL: RMSVoltageV) | RMS Current, A (LGR S/N: 10758121, SEN S/N: 10758121, LBL: RMSCurrentA) | Active Power, W (LGR S/N: 10758121, SEN S/N: 10758121, LBL: ActivePowerW) | Active Energy, Wh (LGR S/N: 10758121, SEN S/N: 10758121, LBL: ActiveEnergyWh) | Apparent Power, VA (LGR S/N: 10758121, SEN S/N: 10758121, LBL: ApparentPowerVA) | Power Factor, PF (LGR S/N: 10758121, SEN S/N: 10758121, LBL: PowerFactorPF) | Host Connected (LGR S/N: 10758121) | Line Loss (LGR S/N: 10758121) | Line Resume (LGR S/N: 10758121) | Stopped (LGR S/N: 10758121) | End Of File (LGR S/N: 10758121)
1 | 2025-11-28 16:12 | 120.66 | 0.8296 | 71.75 | 0 | 100.09 | 0.72
2 | 2025-11-28 16:13 | 120.72 | 0.8214 | 70.48 | 1.18398595 | 99.15 | 0.71
3 | 2025-11-28 16:14 | 120.68 | 0.8143 | 69.4 | 1.16520405 | 98.26 | 0.71
4 | 2025-11-28 16:15 | 120.54 | 0.8073 | 68.36 | 1.14747214 | 97.3 | 0.7 |  | 318000 | 318
5 | 2025-11-28 16:16 | 120.66 | 0.8006 | 67.34 | 1.13241625 | 96.59 | 0.7 |  |  | 0.09433962264
6 | 2025-11-28 16:17 | 120.7 | 0.794 | 66.28 | 1.11088026 | 95.82 | 0.69
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

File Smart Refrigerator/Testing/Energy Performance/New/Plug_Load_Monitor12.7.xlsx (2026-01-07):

Plot Title: Plug Load Monitor
# | Date Time, GMT-08:00 | RMS Voltage, V (LGR S/N: 10758121, SEN S/N: 10758121, LBL: RMSVoltageV) | RMS Current, A (LGR S/N: 10758121, SEN S/N: 10758121, LBL: RMSCurrentA) | Active Power, W (LGR S/N: 10758121, SEN S/N: 10758121, LBL: ActivePowerW) | Active Energy, Wh (LGR S/N: 10758121, SEN S/N: 10758121, LBL: ActiveEnergyWh) | Apparent Power, VA (LGR S/N: 10758121, SEN S/N: 10758121, LBL: ApparentPowerVA) | Power Factor, PF (LGR S/N: 10758121, SEN S/N: 10758121, LBL: PowerFactorPF) | Host Connected (LGR S/N: 10758121) | End Of File (LGR S/N: 10758121)
1 | 2025-12-06 15:04 | 122.93 | 0.0111 | 0.83 | 0 | 1.36 | 0
2 | 2025-12-06 15:05 | 122.96 | 0.0111 | 0.83 | 0.01385747 | 1.36 | 0
3 | 2025-12-06 15:06 | 122.99 | 0.0111 | 0.8 | 0.01366312 | 1.36 | 0
4 | 2025-12-06 15:07 | 122.91 | 0.0111 | 0.84 | 0.01374086 | 1.36 | 0
5 | 2025-12-06 15:08 | 122.84 | 0.0111 | 0.83 | 0.01380564 | 1.36 | 0
6 | 2025-12-06 15:09 | 122.68 | 0.0104 | 0.79 | 0.01339103 | 1.28 | 0
7 | 2025-12-06 15:10 | 122.6 | 0.0104 | 0.84 | 0.01372143 | 1.28 | 0
8 | 2025-12-06 15:11 | 122.61 | 0.0104 | 0.83 | 0.0138769 | 1.28 | 0
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

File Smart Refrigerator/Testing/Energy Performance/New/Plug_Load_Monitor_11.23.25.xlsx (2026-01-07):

Plot Title: Plug Load Monitor
# | Date Time, GMT-08:00 | RMS Voltage, V (LGR S/N: 10758121, SEN S/N: 10758121, LBL: RMSVoltageV) | RMS Voltage - Max, V (LGR S/N: 10758121, SEN S/N: 10758121, LBL: RMSVoltageV) | RMS Voltage - Min, V (LGR S/N: 10758121, SEN S/N: 10758121, LBL: RMSVoltageV) | RMS Voltage - Avg, V (LGR S/N: 10758121, SEN S/N: 10758121, LBL: RMSVoltageV) | RMS Current, A (LGR S/N: 10758121, SEN S/N: 10758121, LBL: RMSCurrentA) | RMS Current - Max, A (LGR S/N: 10758121, SEN S/N: 10758121, LBL: RMSCurrentA) | RMS Current - Min, A (LGR S/N: 10758121, SEN S/N: 10758121, LBL: RMSCurrentA) | Active Power, W (LGR S/N: 10758121, SEN S/N: 10758121, LBL: ActivePowerW) | Active Energy, Wh (LGR S/N: 10758121, SEN S/N: 10758121, LBL: ActiveEnergyWh) | Apparent Power, VA (LGR S/N: 10758121, SEN S/N: 10758121, LBL: ApparentPowerVA) | Power Factor, PF (LGR S/N: 10758121, SEN S/N: 10758121, LBL: PowerFactorPF) | Line Resume (LGR S/N: 10758121) | Host Connected (LGR S/N: 10758121) | End Of File (LGR S/N: 10758121)
1 | 2025-11-22 12:30 | 0 | 0 | 0 | 0 | 0 | 0 | 0 | 0 | 0 | 0 | 0
2 | 2025-11-22 12:31 | 0 | 0 | 0 | 0 | 0 | 0 | 0 | 0 | 0 | 0 | 0
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

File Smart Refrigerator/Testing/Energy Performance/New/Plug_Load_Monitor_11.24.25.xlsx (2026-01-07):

Plot Title: Plug Load Monitor
# | Date Time, GMT-08:00 | RMS Voltage, V (LGR S/N: 10758121, SEN S/N: 10758121, LBL: RMSVoltageV) | RMS Current, A (LGR S/N: 10758121, SEN S/N: 10758121, LBL: RMSCurrentA) | Active Power, W (LGR S/N: 10758121, SEN S/N: 10758121, LBL: ActivePowerW) | Active Energy, Wh (LGR S/N: 10758121, SEN S/N: 10758121, LBL: ActiveEnergyWh) | Apparent Power, VA (LGR S/N: 10758121, SEN S/N: 10758121, LBL: ApparentPowerVA) | Power Factor, PF (LGR S/N: 10758121, SEN S/N: 10758121, LBL: PowerFactorPF) | Line Resume (LGR S/N: 10758121) | Host Connected (LGR S/N: 10758121) | Line Loss (LGR S/N: 10758121) | End Of File (LGR S/N: 10758121)
1 | 2025-11-22 12:30 | 0 | 0 | 0 | 0 | 0 | 0
2 | 2025-11-22 12:31 | 0 | 0 | 0 | 0 | 0 | 0
3 | 2025-11-22 12:31 | 0 | 0 | 0 | 0 | 0 | 0
4 | 2025-11-22 12:32 | 0 | 0 | 0 | 0 | 0 | 0
5 | 2025-11-22 12:32 | 0 | 0 | 0 | 0 | 0 | 0
6 | 2025-11-22 12:33 | 0 | 0 | 0 | 0 | 0 | 0
7 | 2025-11-22 12:33 |  |  |  |  |  |  | Logged
8 | 2025-11-22 12:33 | 122.24 | 0.9111 | 84.87 | 0.65759593 | 111.36 | 0.76
9 | 2025-11-22 12:34 | 122.29 | 0.8662 | 78.21 | 0.67513734 | 105.91 | 0.74
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

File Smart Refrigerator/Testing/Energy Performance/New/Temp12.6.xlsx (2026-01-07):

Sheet: Data
# | Date-Time (PST) | Temperature , °C | RH , % | Dew Point , °C
1 | 2025-11-25 17:21 | 17.87 | 55.85 | 8.95
2 | 2025-11-25 17:22 | 18.11 | 57.15 | 9.51
3 | 2025-11-25 17:23 | 18.41 | 55.66 | 9.40
4 | 2025-11-25 17:24 | 19.22 | 55.63 | 10.15
5 | 2025-11-25 17:25 | 19.62 | 48.59 | 8.50
6 | 2025-11-25 17:26 | 19.47 | 49.82 | 8.74
7 | 2025-11-25 17:27 | 19.20 | 52.96 | 9.39
8 | 2025-11-25 17:28 | 18.92 | 51.92 | 8.84
9 | 2025-11-25 17:29 | 18.72 | 53.40 | 9.07
10 | 2025-11-25 17:30 | 18.55 | 52.76 | 8.74
11 | 2025-11-25 17:31 | 18.43 | 53.50 | 8.83
12 | 2025-11-25 17:32 | 18.33 | 54.34 | 8.97
13 | 2025-11-25 17:33 | 18.26 | 54.80 | 9.03
14 | 2025-11-25 17:34 | 18.22 | 54.83 | 9.00
15 | 2025-11-25 17:35 | 18.17 | 55.05 | 9.01
16 | 2025-11-25 17:36 | 18.15 | 54.82 | 8.93
17 | 2025-11-25 17:37 | 18.14 | 55.06 | 8.99
18 | 2025-11-25 17:38 | 18.15 | 55.44 | 9.10
19 | 2025-11-25 17:39 | 18.16 | 55.34 | 9.08
20 | 2025-11-25 17:40 | 18.20 | 55.35 | 9.12
21 | 2025-11-25 17:41 | 18.22 | 55.13 | 9.09
22 | 2025-11-25 17:42 | 18.24 | 55.80 | 9.28
23 | 2025-11-25 17:43 | 18.27 | 54.94 | 9.08
24 | 2025-11-25 17:44 | 18.30 | 54.74 | 9.05
25 | 2025-11-25 17:45 | 18.32 | 54.70 | 9.06
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

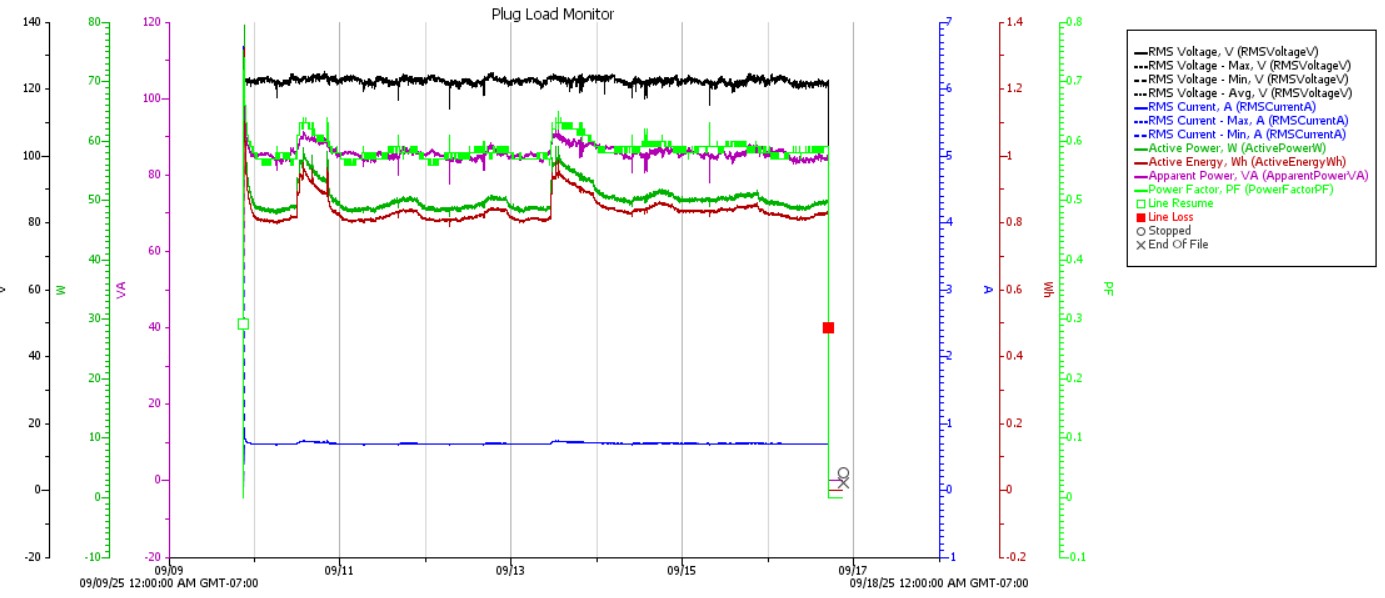
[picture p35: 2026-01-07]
Smart Refrigerator/Testing/Energy Performance/Level 5 Power/Level5.jpg

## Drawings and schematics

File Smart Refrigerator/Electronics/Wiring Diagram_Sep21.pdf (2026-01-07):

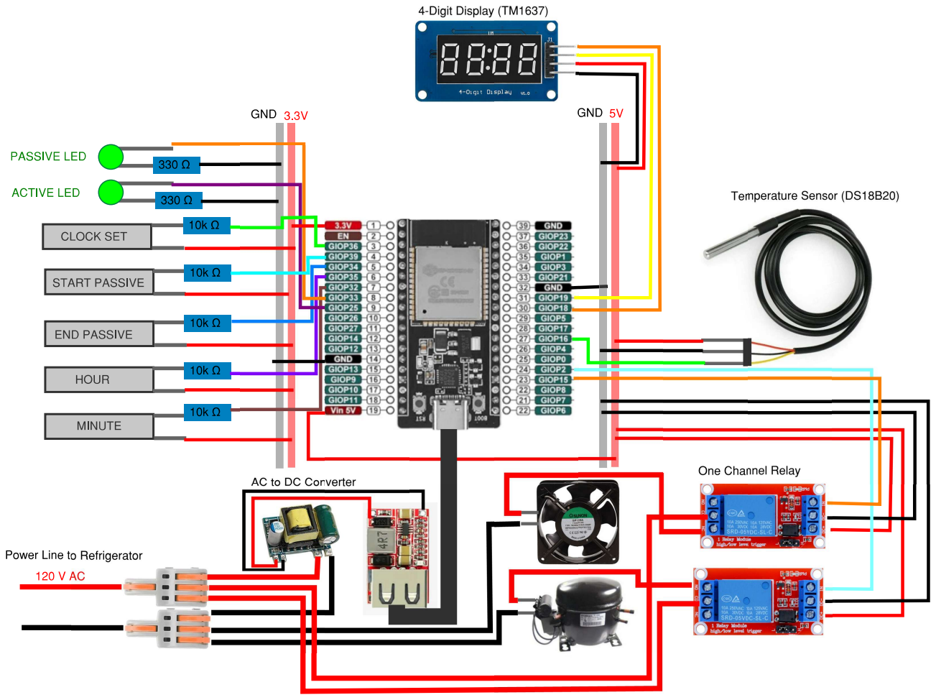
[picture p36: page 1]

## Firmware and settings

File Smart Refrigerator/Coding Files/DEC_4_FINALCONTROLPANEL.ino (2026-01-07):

#include <TM1637Display.h>
#include <OneWire.h>
#include <DallasTemperature.h>
#include <Wire.h>
#include "RTClib.h"

#define ONE_WIRE_BUS 16
#define CLK 22
#define DIO 23
#define TEMPFLASH 27
#define HOUR_B 13
#define MINUTE_B 14
#define CLOCKSET 19
#define END_P 4
#define Pass_Pin 32
#define Act_Pin 33
#define RelayFan 15
#define RelayCom 2

RTC_DS3231 rtc;

TM1637Display display(CLK, DIO);
OneWire oneWire(ONE_WIRE_BUS);
DallasTemperature sensors(&oneWire);

int startHour = 0;    
int startMinute = 0;  
int hours = 0;
int minutes = 1;
bool clkTrigger = false;
bool running = false;
bool countdownTrigger = false;
bool autoOverride = false;
int lastMinute = -1;
float temp = 0.0;
unsigned long previousMillis = 0;
bool fanArmed = true;

// ---- ADDED ---- Temperature smoothing + fan latch
float smoothTemp = 0;
unsigned long fanOnLatchUntil = 0;

// ★ Fixed safe switching logic — prevents relay chatter
void safeRelaySwitch(int relayPin, bool newState) {
  bool oldState = digitalRead(relayPin);

  // No change, no action
  if (oldState == newState) return;

  // Enforce 1-second buffer before a real state change
  delay(1000);

  // Perform switch once
  digitalWrite(relayPin, newState);
}

void setup() {
  pinMode(HOUR_B, INPUT_PULLUP);
  pinMode(MINUTE_B, INPUT_PULLUP);
  pinMode(TEMPFLASH, INPUT_PULLUP);
  pinMode(CLOCKSET, INPUT_PULLUP);
  pinMode(END_P, INPUT_PULLUP);
  pinMode(Pass_Pin, OUTPUT);
  pinMode(Act_Pin, OUTPUT);
  pinMode(RelayFan, OUTPUT);
  pinMode(RelayCom, OUTPUT);

  sensors.begin();
  display.setBrightness(0x0f);
  updateDisplay();

  Wire.begin(18, 21);
  if (!rtc.begin()) {
    Serial.println("Couldn't find RTC");
    while (1);
  }
}

void updateDisplay() {
  int displayTime;
  if (running) {
    displayTime = hours * 100 + minutes;
  }
  else if (clkTrigger) {
    displayTime = hours * 100 + minutes;
  }
  else {
    displayTime = startHour * 100 + startMinute;
  }
  display.showNumberDecEx(displayTime, 0b01000000, true);
}

void countDown() { 
  if (minutes > 0) {
    minutes--;
  } else if (hours > 0) {
    hours--;
    minutes = 59;
  } else {
    running = false;
    digitalWrite(Pass_Pin, LOW);
    digitalWrite(Act_Pin, HIGH);

    safeRelaySwitch(RelayFan, LOW);
    safeRelaySwitch(RelayCom, HIGH);
  }
}

void toggleFan() {
  sensors.requestTemperatures(); 
  float rawTemp = sensors.getTempFByIndex(0);

  // ---- EMA Temperature smoothing ----
  smoothTemp = 0.9 * smoothTemp + 0.1 * rawTemp;

  bool fanState = digitalRead(RelayFan);
  unsigned long now = millis();

  // If COM is on, fan must be off
  if (digitalRead(RelayCom) == HIGH) {
    if (fanState == HIGH) safeRelaySwitch(RelayFan, LOW);
    fanArmed = true;
    return;
  }

  // ---- Fan ON latch (prevents rapid re-triggering) ----
  if (now < fanOnLatchUntil) return;

  // FIRST trigger: turn fan ON once at >= 40°F
  if (fanArmed && smoothTemp >= 40.0) {
    safeRelaySwitch(RelayFan, HIGH);
    fanArmed = false;
    fanOnLatchUntil = now + 10000; // 10 second lockout
    return;
  }

  // SECOND trigger: turn fan OFF once at <= 37°F
  if (!fanArmed && smoothTemp <= 37.0) {
    safeRelaySwitch(RelayFan, LOW);
    fanArmed = true;
    return;
  }
}

void flashTemperature() {
  sensors.requestTemperatures();
  float t = sensors.getTempFByIndex(0);
  int tempInt = (int)t;

  unsigned long startTime = millis();

  while (millis() - startTime < 3000) {
    display.showNumberDec(tempInt, true);
    delay(500);
    display.clear();
    delay(500);
  }

  updateDisplay();
}

void loop() {   
  DateTime now = rtc.now();
  int currentHour = now.hour();
  int currentMinute = now.minute();

  if (now.minute() != lastMinute) {
    autoOverride = false;
    lastMinute = now.minute();
  }

  if (digitalRead(TEMPFLASH) == LOW) {
    delay(200);
    flashTemperature();
  }

  if (!autoOverride && !countdownTrigger && !running &&
      currentHour == startHour && currentMinute == startMinute) {
        
    hours = hours;
    minutes = minutes;
    running = true;
    countdownTrigger = true;
    clkTrigger = false;

    digitalWrite(Pass_Pin, HIGH);
    digitalWrite(Act_Pin, LOW);

    safeRelaySwitch(RelayCom, LOW);
  }

  // SYSTEM IDLE
  else if (!running) {
    digitalWrite(Pass_Pin, LOW);
    digitalWrite(Act_Pin, HIGH);

    safeRelaySwitch(RelayFan, LOW);
    safeRelaySwitch(RelayCom, HIGH);
  }

  if (!running) countdownTrigger = false;

  if (digitalRead(HOUR_B) == LOW && !clkTrigger) {
    delay(200);
    startHour = (startHour + 1) % 24;
    updateDisplay();
  }

  if (digitalRead(HOUR_B) == LOW && clkTrigger) {
    delay(200);
    hours = (hours + 1) % 24;
    updateDisplay();
  }

  // SET AUTO START MINUTE
  if (digitalRead(MINUTE_B) == LOW && !clkTrigger) {
    delay(200);
    startMinute = (startMinute + 1) % 60;
    updateDisplay();
  }

  if (digitalRead(MINUTE_B) == LOW && clkTrigger) {
    delay(200);
    minutes = (minutes + 1) % 60;
    updateDisplay();
  }

  if (digitalRead(CLOCKSET) == LOW) {
    delay(200);
    clkTrigger = true;
  }

  if (digitalRead(END_P) == LOW) {
    delay(200);
    autoOverride = true;
    running = false;
    clkTrigger = false;

    digitalWrite(Pass_Pin, LOW);
    digitalWrite(Act_Pin, HIGH);

    safeRelaySwitch(RelayFan, LOW);
    safeRelaySwitch(RelayCom, HIGH);

    fanArmed = true;
    updateDisplay();
  }

  if (running) {
    unsigned long currentMillis = millis();
    if (currentMillis - previousMillis >= 60000) {
      previousMillis = currentMillis;
      countDown();
      updateDisplay();
    }
    toggleFan();
  } else {
    safeRelaySwitch(RelayFan, LOW);
    safeRelaySwitch(RelayCom, HIGH);
    fanArmed = true;
  }
}
